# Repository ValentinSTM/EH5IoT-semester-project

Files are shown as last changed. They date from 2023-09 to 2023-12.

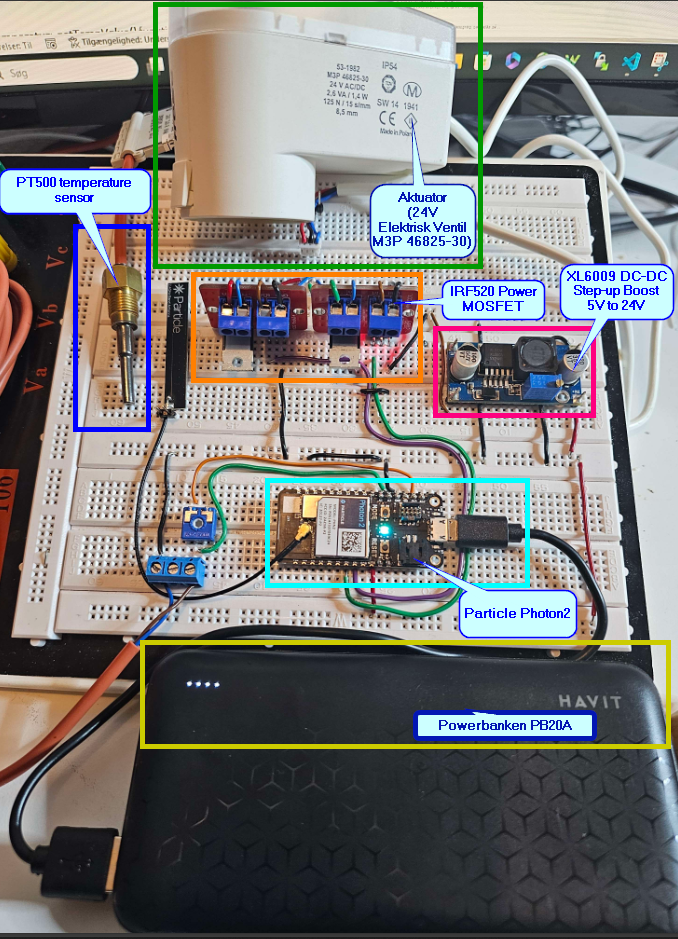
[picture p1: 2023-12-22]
Docs_Tests/Realisering-.png

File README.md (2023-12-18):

# EH5IoT-semester-project
The IoT semester project - Return Temperature Regulation for Fjernvarme
## Table of Contents
- [General Info](#general-info)
- [Technologies](#technologies)
- [Requirements](#requirements)
  - [Functional Requirements](#functional-requirements)
  - [Non-functional Requirements](#non-functional-requirements)

## General Info
This project focuses on optimizing the return temperature in Heating System District ( Fjernvarme ) to enhance energy efficiency and promote environmental sustainability. In collaboration with Kredsløb A/S, we strive to maintain return temperatures below 30°C, which qualifies for a bonus.

"Få styr på din fjernvarme og spar penge på din varme

Vidste du, at du kan spare penge på din varmeregning og samtidig bidrage til mere klimavenlig fjernvarme? Hemmeligheden ligger i det, der hedder returtemperatur og god udnyttelse af energien.
Det er temperaturen på det fjernvarmevand, der bliver sendt retur fra dit hjem til varmeværket.
Og er returtemperatur fra din bolig under 30°C, får du en bonus." (www.kredslob.dk)

### About Fjernvarme
Fjernvarme is a district heating system that supplies heat to multiple households from a centralized source. The return temperature refers to the temperature of the water sent back from homes to the heating plant.

### Project Implementation
This system was implemented using one Particle Photon2 board, leveraging IoT technology to gather data from weather forecasts webhook and changing temperature setpoint after those data as seen in the tabel. 
Logic for temperature setpoint is dynamic depending on the outside temperature.

| Temperature Condition | Set Point  |
|---|---|
| Extreme low temperature (< -3°C) | 40°C |
| Low temperature (-2°C to 2°C) | 35°C |
| Normal temperature (> 3°C) | 30°C |

The system will collect data from a temperature sensor RTD PT500 Kamstrup mounted on return pipe .
Data collected from the temperature sensor will by used in an PID controller (Proportional, Integral, Derivative ) able to control the dynamic system, by giving som resultat a parameter to adjust the position of an electro valve. 
- P = Proportional - Kp = Proportional constant (adjust current error)
- I = Integral - Ki = Integral constant ( adjust past error)
- D = Derivative - Kd = Derivative constant (adjust future error)

## Technologies
The following technologies are used in this project:
- Particle Photon2 for data acquisition and actuator control
- Temperature Sensor: PT500 Kamstrup
- Actuator: 24V Electric Valve M3P 46825-30
- IoT: Webhooks for weather forecast data

## Requirements
### Functional Requirements
The device must meet the following functional requirements:
- Establish an internet connection via Wi-Fi
- Read data from the connected PT500 temperature sensor
- Control the electric valve actuator
- Utilize data from a web service, such as weather forecast data to help in controlling the system.

### Non-functional Requirements

- Create a public GitHub account and upload relevant project files.
- Upload hardware documentation, schematics, datasheets, and optional PCB layouts in PDF format.
- Upload software files in raw source code format, such as .C, .CPP, .h, .py, etc.

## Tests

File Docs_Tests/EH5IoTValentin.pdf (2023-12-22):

# Valentin-Stefan Tudora-Mayer Studienummer: 202104813

# EH5 IoT projekt

# Optimering af returtemperatur i fjernvarmesystemer ved brug af IoT-teknologi

### S i d e 1 | 24

Dato: 21. december 2023

Kursus: EH5IoT
Navn / Studienummer:
Valentin-Stefan Tudora-Mayer / 202104813

## Indhold

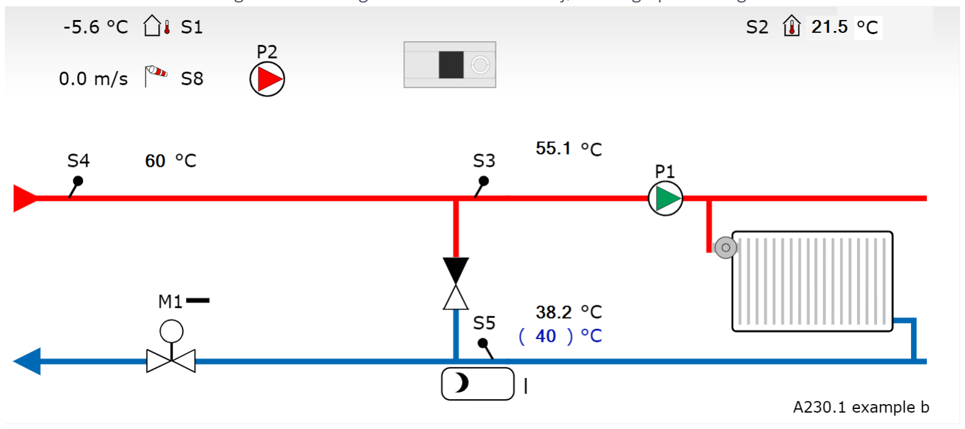
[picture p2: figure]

### S i d e 2 | 24

## Introduktion

Dette projekt, EH5IoT-semesterprojektet, koncentrerer sig om optimering af returtemperaturen i fjernvarmesystemer for at øge energieffektiviteten og fremme bæredygtighed. Samarbejdet med Kredsløb A/S understreger vores mål om at opretholde returtemperaturer under 30°C, hvilket kvalificerer til en økonomisk bonus. Vores initiativ adresserer det voksende behov for klimavenlige løsninger i fjernvarmesektoren, et kritisk element i overgangen til mere bæredygtige energisystemer.

Målet med EH5IoT-semesterprojektet er at anvende Internet of Things (IoT)-teknologi for at præcist regulere og optimere returtemperaturen i fjernvarmesystemer. Ved at integrere avanceret sensorik og intelligent styring, sigter vi mod at forbedre systemets samlede energieffektivitet, reducere driftsomkostninger for slutbrugere og bidrage til et mere miljømæssigt ansvarligt fjernvarmesystem.

Løsningen involverer implementering af et IoT-baseret system, der bruger Particle Photon2-board til at indsamle data og styre en aktuator. Systemet vil anvende data fra vejrprognoser til dynamisk at justere setpunkterne for returtemperaturen, baseret på udendørs temperaturforhold. Ved hjælp af en RTD PT500 Kamstrup-temperatursensor monteret på returrøret, vil systemet indsamle nøjagtige data, der bruges af en PID-controller (Proportional, Integral, Derivative) til at styre en elektrisk ventil effektivt. Denne innovative tilgang tillader præcis kontrol og tilpasning af systemet i realtid, hvilket øger effektiviteten og understøtter en mere bæredygtig energianvendelse.

## Projektbeskrivelse

Fjernvarme er et centraliseret varmesystem, der leverer varme til flere husstande. I dette system er returtemperaturen
- temperaturen på vandet, der sendes tilbage fra boligerne til varmeværket - afgørende for systemets effektivitet. En lavere returtemperatur betyder, at mere varme er blevet udnyttet i boligerne, hvilket fører til en højere effektivitet og lavere energiforbrug.

I dette projekt, i samarbejde med Kredsløb A/S, er der et specifikt fokus på at opretholde returtemperaturen på 30°C, mens indgangstemperaturen, der garanteres af Kredsløb A/S, er på 60°C (Figur 1). Dette temperaturinterval er afgørende for at sikre maksimal udnyttelse af den leverede varmeenergi. For eksempel, en reduktion i returtemperaturen fra 35°C til 30°C, mens indgangstemperaturen forbliver på 60°C, betyder en forbedring i energieffektiviteten.

Optimeringen af returtemperaturen er derfor afgørende for at forbedre fjernvarmesystemets overordnede energieffektivitet og for at reducere de miljømæssige påvirkninger.

Figur 1 [1]Fjernvarme flowdiagram (Kilder - Kredsløb A/S - ECL portal)

### S i d e 3 | 24

### Beskrivelse af systemets hovedkomponenter

Systemet blev udviklet til dette formål og omfatter flere nøglekomponenter:

1. Particle Photon2: Dette er en mikrocontroller, der fungerer som kernen i IoT-løsningen. Den indsamler data fra forskellige sensorer og styrer aktuatorer baseret på foruddefinerede logikker og eksterne datainput. En afgørende funktion ved Particle Photon2 er dens evne til at forbinde til internettet, hvilket muliggør fjernovervågning og -styring af systemet. Takket være Particles integrerede cloud-tjenester, kan systemet nemt tilgå og anvende data fra eksterne kilder, såsom vejrprognoser, hvilket spiller en nøglerolle i projektet. Denne forbindelse til internettet udvider systemets funktionalitet betydeligt og tillader en mere fleksibel og effektiv styring af fjernvarmesystemet.
2. Temperatursensor PT500 Kamstrup: Denne sensor er monteret på returrøret og måler returtemperaturen med præcision. Disse data er afgørende for at regulere og vedligeholde den optimale returtemperatur.
3. Aktuator (24V Elektrisk Ventil M3P 46825-30): Denne bruges til at justere vandstrømmen og dermed returtemperaturen baseret på data og kommandoer fra Particle Photon2 og PID-controlleren.

Logikken implementeret for temperaturregulering.
Systemet anvender en dynamisk logik til temperaturregulering, som er afhængig af eksterne temperaturforhold. En PID-controller (Proportional, Integral, Derivative) anvendes, som justerer ventilens position for at opnå den ønskede returtemperatur. Controlleren modtager input fra temperatursensoren og justerer aktivt ventilen baseret på tre parametre:
- Proportional (P): Justerer den aktuelle fejl.
- Integral (I): Akkumulerer tidligere fejl for at forbedre stabilitet over tid.
- Derivative (D): Forudsiger fremtidige fejl og reagerer på ændringer.

Ved at integrere realtidsdata fra sensorer og vejrprognoser, kan systemet proaktivt justere set punkterne for returtemperaturen, hvilket sikrer maksimal effektivitet under alle driftsforhold.

## Kravs analyse

Krav
ID | Kategori | Beskrivelse

Godkendt/Ikke
godkendt | Kommentarer
F.1 | Funktionelt

Enheden skal forbinde til internettet via
WiFi. | Godkendt

AU's "AU Gadget netværk" er testet og fungerer.

F.2 Funktionelt

Enheden skal aflæse data fra PT500-
sensoren, som måler temperatur og
implementerer datatfiltrering. | Godkendt

PT500 sensoren er
implementeret og funktionalitet bekræftet via tests.

F.3 Funktionelt

Enheden skal kunne styre en aktuator,
som er reguleret af en PID-controller. Godkendt

PID-reguleringen er
implementeret og justeret
baseret på tests.

### S i d e 4 | 24

Krav
ID | Kategori | Beskrivelse

Godkendt/Ikke
godkendt | Kommentarer
F.4 | Funktionelt

Enheden skal integrere og anvende data
fra eksterne webtjenester til at forbedre
dens funktionalitet. | Godkendt

Integration af webhooks og API'er for vejrdata er testet og implementeret.

F.5 Funktionelt

Data skal sendes til clouden i en log med
defineret interval og størrelse for at
monitorere systemets ydeevne. | Godkendt

Data logning og transmission er implementeret og fungerer som forventet.

F.6 Funktionelt

Aktuatoren skal kunne modtage strøm
fra en batterikilde ved hjælp af en DC-DC
boost step-up konverter. | Godkendt

Implementeringen og tests af DC-DC konverteren har bekræftet korrekt funktion.

IF.1

Ikke-funktionelt

Offentlig GitHub-repository med alle
relevante filer. | Godkendt

Repository er aktivt og offentligt tilgængeligt.

IF.2

Ikke-funktionelt

Hardware dokumentation inklusiv
skematikker og datablade skal uploades i
PDF-format. | Godkendt

Komplet dokumentation er
tilgængelig og godkendt.

IF.3

Ikke-funktionelt

Software kildekoden skal uploades i rå
format. | Godkendt

Kildekoden er tilgængelig i repository og er blevet
gennemgået.

T.1 Teknisk

Den indlejrede platform skal være en
Particle-enhed med WiFi-forbindelse. | Godkendt | Particle-enhed valgt og testet.
T.2 | Teknisk

Platformen skal have digitale/analoge
I/O'er for sensor- og
aktuatorforbindelser. | Godkendt

I/O-specifikationer er opfyldt og fungerer som forventet.

T.3 Teknisk

Systemet skal kunne drives af batteri, ud
over USB 5V strømforsyning. | Godkendt

Batteridrift er testet og klar til yderligere overvågning for at optimere levetiden.

T.4 Teknisk

Batteriets levetid og systemets samlede energiforbrug skal evalueres for at
estimere driftstiden ved fuld
batteriopladning. | Godkendt

Yderligere langvarige tests og overvågning nødvendige for at fastlægge nøjagtig batterilevetid.

Bemærk, at selvom alle kravene er markeret som "Godkendt", indikerer kommentaren for T.4, at der stadig er behov for yderligere langvarige tests og overvågning for præcist at bestemme batteriets levetid, især fordi aktuatoren har et højere strømforbrug under drift, hvilket er kritisk for den overordnede energieffektivitet og anvendelighed af systemet i områder uden elektrisk strømforsyning.

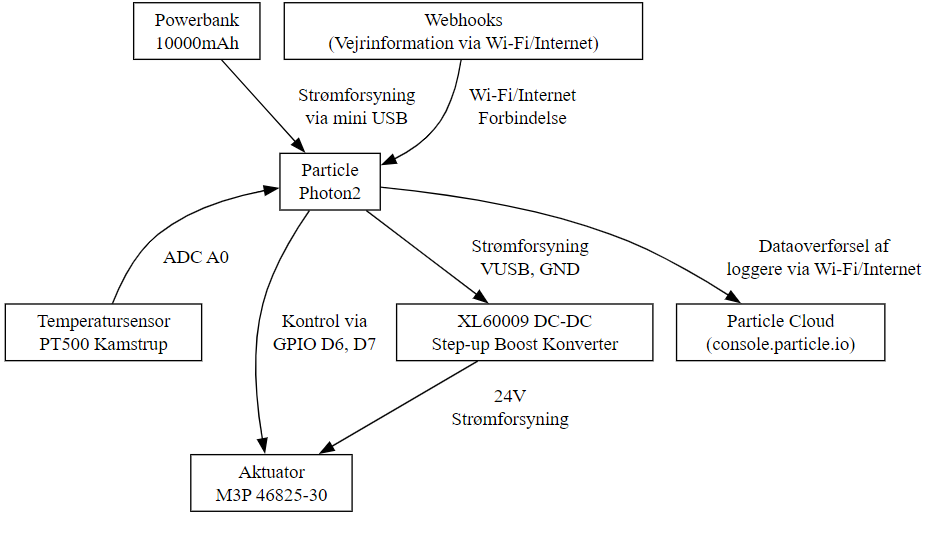
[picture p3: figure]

### S i d e 5 | 24

## Systemdesign

Systemets diagram.

Figur 2 System Block Diagram

## Hardware

- Particle Photon2 (Figur 3 og Figur 4 [2]) er en avanceret mikrocontroller modul designet til Internet of Things (IoT) applikationer som tilbyder :
- MCU & Processor: Realtek RTL8721DM, ARM Cortex M33, 200 MHz.
- Hukommelse: 2 MB Flash, 3 MB RAM.
- Wi-Fi: Dual-band 2.4 GHz & 5 GHz, BLE 5 support.
- Antenne: Integreret PCB, U.FL for ekstern antenne.
- I/O Porte: 6x ADC, 3x UART, 2x SPI, I2C-kommunikation.
- Strømstyring: Understøtter LiPo-batteri, USB-strøm.
- Lavenergimodes: Effektive sleep modes for strømbesparelse.
- Firmware: Over-the-air opdateringer, Device OS 5.0.0+.

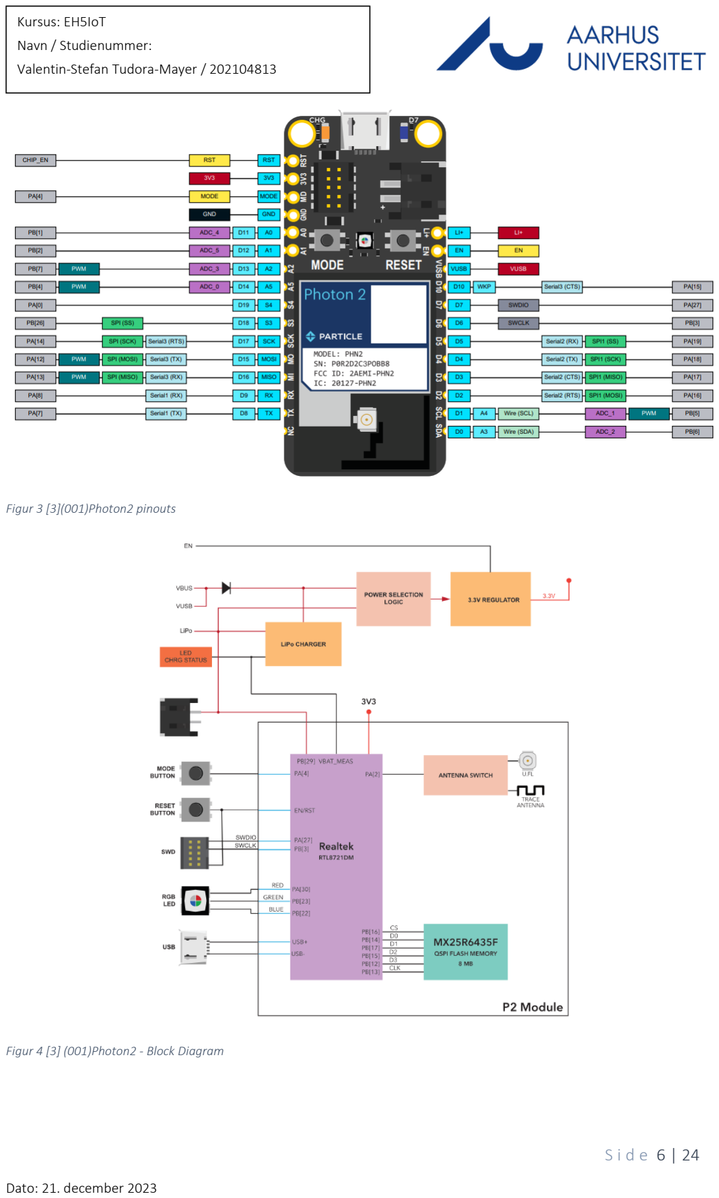
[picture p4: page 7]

### S i d e 6 | 24

Figur 3 [3](001)Photon2 pinouts

Figur 4 [3] (001)Photon2 - Block Diagram

### S i d e 7 | 24

- PT500 er en 2-leder resistiv temperaturføler(Figur 6), anvendt til nøjagtig måling af temperaturen i fjernvarmesystemer. PT500 temperaturføleren, ofte anvendt i varme- og kølesystemer, bruger tyndfilmsmodstande monteret på et trykt kredsløbskort (PCB). Tyndfilmsmodstande er valgt for deres omkostningseffektivitet, kompakthed og hurtige respons på temperaturændringer. Denne konstruktion tillader massekproduktion og reducerer omkostninger. Med loddeøer på PCB, er det let at forbinde to ledninger til en 2-leder temperaturføler, hvilket optimerer fremstillingsprocessen. PT500 sensoren kan typisk bruges op til 150 °C, hvilket er tilstrækkeligt for de fleste installationer.
Sensoren har følgende karakteristika:
- Modstandsændring: Sensoren benytter platin med en temperaturkoefficient på 0,00385 ohm/ohm/°C, hvilket sikrer en præcis og næsten lineær respons til temperaturændringer.
- Tabelbaseret beregning: Til konvertering af modstandsværdier til temperaturer anvendes en standardtabel, som er integreret i systemets software. Dette sikrer en høj grad af nøjagtighed i temperaturbestemmelsen.
- 2-leder konfiguration: Selvom PT500 også er tilgængelig i 4-leder konfigurationer for endnu større nøjagtighed, anvendes en 2-leder konfiguration i dette projekt

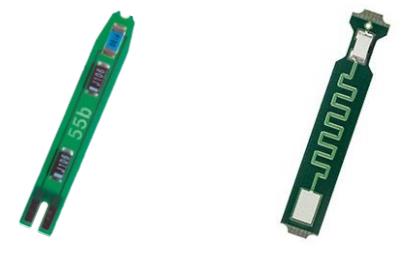
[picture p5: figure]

Figur 5 [3](002)Tyndfilmsmodstande, som er monteret på et PCB (printed circuit board)

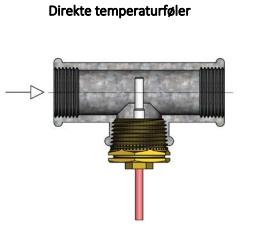
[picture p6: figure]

Figur 6 [3](002)Illustration af en direkte temperaturføler

### S i d e 8 | 24

- M3P 46825-30 aktuatoren (Figur 7)er en motoriseret aktuator til regulering af flow i varme- og kølesystemer. Tekniske specifikationer inkluderer:
- Kontroltype: 3-punkts kontrol uden feedback.
- Driftsspænding: 24 V AC, -10 % ... +20 %, 50-60 Hz 24 V DC, -20 % ... +20 %
- Driftseffekt: 0,2 W...1,4 W (DC), 0,56 VA...2,6 VA (AC)
- Strømforbrug (M3P): < 110 mA
- Indstillingsvej: 8,5 mm
- Indstillingskraft: 100/125/150/200 N -20 % ... +40 %
- Indstillingstid: 15s, 30s s/mm
- Omgivelsestemperatur: 0 °C ... +50 °C
- Beskyttelsesklasse: IP 54 i henhold til EN 60529.
- Kontrolsignal: 3-punkts signal.
- Denne aktuator er central i projektet for at præcist justere ventilpositionen, hvilket direkte påvirker returtemperaturen i opvarmningssystemet, og bidrager til at forbedre systemets energieffektivitet.

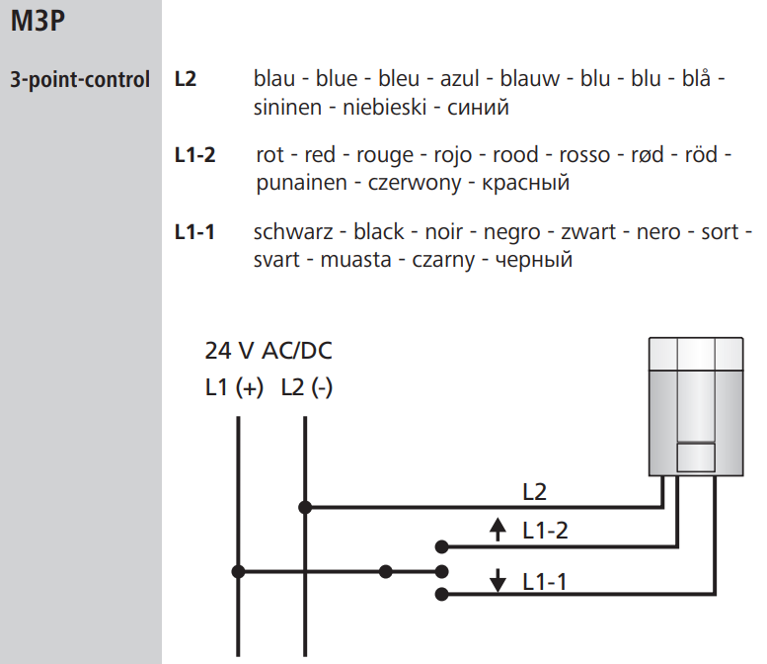
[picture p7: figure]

Figur 7 [3](003) Elektrisk diagram

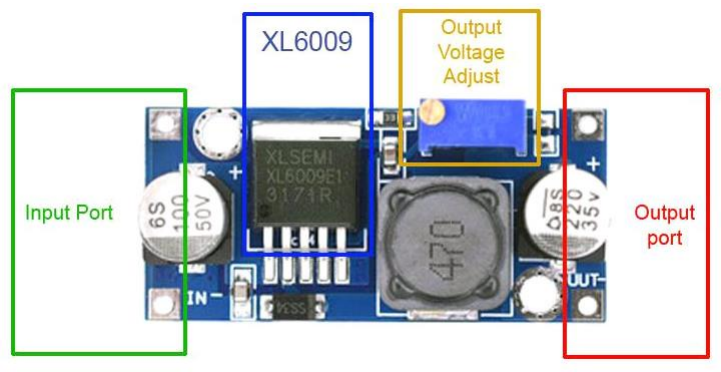
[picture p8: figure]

### S i d e 9 | 24

- Powerbanken PB20A (Figur 8), anvendt i projektet, til at forsyne med strøm , har følgende nøgleegenskaber:
- Kapacitet: 10.000 mAh, 3,7 V, 37 Wh, hvilket sikrer tilstrækkelig strøm til langvarig brug af systemet.
- Indgang og Udgang: Udstyret med USB-C-indgang (5 V/2 A) og USB-A-udgang (5 V/2 A), der tilbyder alsidige opladningsmuligheder og høj kompatibilitet med forskellige enheder.
- Sikkerhedsfunktioner: Inkluderer overladningsbeskyttelse og automatisk slukning efter fuld opladning, hvilket sikrer både powerbankens og tilkoblede enheders sikkerhed.

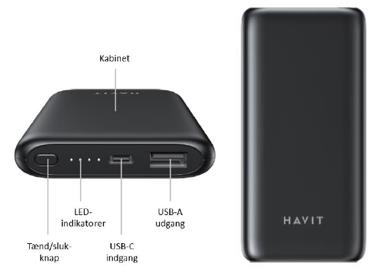
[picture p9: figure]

Figur 8 [3](004) Powerbank

- XL6009 DC-DC (Figur 9): Specifikationer og egenskaber for strømmodul til at levere strøm til en 24V aktuator:
- Indgangsspænding: 3 - 32V.
- Udgangsspænding: Justerbar fra 5 - 35V.
- Udgangsstrøm: Maksimal udgangsstrøm 4A. Bemærk: Jo højere spændingen er, desto større bliver belastningsstrømmen.
- Effektivitet: Op til <94% effektivitet.
- Belastningsregulering: 0,5%.
- Spændingsregulering: 0,5%.
- Justerbar potentiometer: Ombord for justering af udgangsspændingen.

Figur 9 [3] (005) XL6009 DC-DC Convertor module

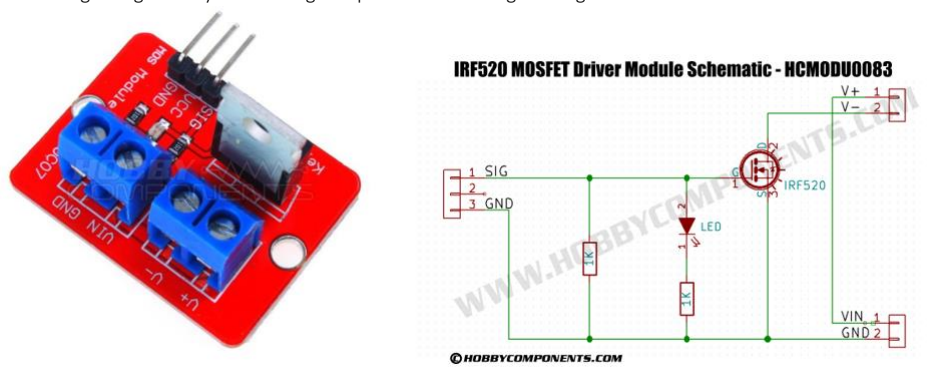
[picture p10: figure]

### S i d e 10 | 24

- IRF520 (Figur 10) Power MOSFET N-Channel modulen benytter en IRF520 Power MOSFET for at styre og regulere PWM-signaler til belastninger som DC-motorer og magnetventiler.
- Modulen kan håndtere en udgangsspænding på 0-24V og en udgangsstrøm på op til 9,5A. For strømme over 1A kræves en ekstra køleplade. Den understøtter gate-spændingssignaler på både 3,3V og 5V og er forsynet med digitale porte til niveau-signalering.

Figur 10 [4](006) IRF520 Modulen og Skematik

Grænseflade og kommunikation mellem komponenter.

## Implementering

Udviklingsprocessen for hardware og software.
Implementeringsfasen i EH5IoT-projektet omhandler integration og konfiguration af hardware og softwarekomponenter for at skabe et fungerende IoT-system som skal afleveres en retur temperatur som er indstillet på setpoint.

Det inkluderer etablering af forbindelser mellem komponenter som Particle Photon2, PT500 temperatursensoren, M3P 46825-30 aktuatoren, powerbanken , XL6009 DC-DC konverteren og IRF520 Power MOSFET. Under denne fase er der lagt vægt på at sikre korrekt energioverførsel, dataindsamling og -behandling samt effektiv kommunikation mellem systemets dele. Desuden er der udviklet software til at styre og regulere systemet baseret på realtidsdata og prædefinerede algoritmer.

Prototypen til projektet blev udviklet på et eksperimentbræt (breadboard), hvor en PCB ikke var nødvendig. Systemets strømforsyning kommer fra en powerbank, der leverer 5V via USB til Particle Photon2-platformen. Fra Particle Photon2's Vusb-pin leveres strøm til XL6009 DC-DC-modulet, som konverterer spændingen op til de nødvendige 24V for aktuatoren M3P 46825-30. Alternativt kunne en SAFT longlife-batteri bruges, der ofte anvendes i fjernvarmeapplikationer og industrielle miljøer.

Aktuatoren styres digitalt fra Photon2's pins D6 og D7, via to IRF520 Power MOSFET-moduler, som understøtter gate-spændingssignaler på 3,3V og 5V og kan håndtere en udgangsspænding på 0-24V og en udgangsstrøm på op til 9,5A. Temperaturen setpoint styres dynamisk baseret på vejrprognoser hentet via en webhook, med sætpunkter på 30, 35 eller 40 °C.

Temperature Condition | Set Point
Extreme low temperature (< -3°C) | 40°C
Low temperature (-2°C to 2°C) | 35°C
Normal temperature (> 3°C) | 30°C
Tabel 1 Setpoint temperature

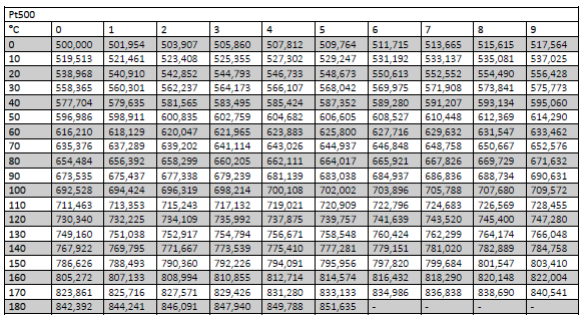
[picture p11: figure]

### S i d e 11 | 24

Returtemperaturen registreres ved hjælp af en PT500 temperatursensor, som er tilsluttet mellem A0-pinden på en Photon2, GND, og en 1k Ohm variabel modstand. Dette setup gør det muligt at beregne resistansen af PT500-sensoren. PID-regulatoren tilpasser herefter aktuatoren bevægelserne for at holde den ønskede temperatur, baseret på feedback fra PT500-sensoren. Værdien af Pt500 beregnes ved brug af en tabel (Tabel 2) over resistansværdier, som svarer til forskellige temperaturer, leveret af sensorens producent, Kamstrup A/S.

Tabel 2 [3] - Pt500, IEC 751 Amendment 2-1995-07

Hardware

Figur 11 Implementering skematik


### S i d e 12 | 24

Software

Softwarekomponenterne i projektet arbejder sammen for at regulere og overvåge fjernvarmesystemets returtemperatur. Kernen i softwarelogikken er en PID-controller, som dynamisk justerer en aktuators position baseret på feedback fra en PT500 temperatursensor. Temperaturen læses og jævnes ud gennem en glidende gennemsnitsfunktion for at sikre stabil drift.

Vigtige funktioner i softwaren omfatter indsamling af temperaturdata, kommunikation med vejrprognoser og systemets interaktion med Particle Cloud for at logge og overvåge ydeevnen. PID-controllerens konstanter (Kp, Ki, Kd) er defineret for at balancere systemets respons mellem nuværende, akkumuleret og forventet temperaturafvigelse. Systemet håndterer også intervalbaserede opgaver som indsamling og offentliggørelse af data samt opdatering af setpoint temperature baseret på vejrforudsigelser som er beskrevet i Tabel 1.

Hele implementeringen er trådbaseret for at sikre kontinuerlig og uafhængig håndtering af de forskellige systemopgaver. Koden er skrevet i C++ og gør brug af Particle's udviklingsmiljø og biblioteker. For detaljeret gennemgang og yderligere teknisk indsigt, kan koden tilgås på GitHub [5].

Figur 12Forsimplet Software Diagram

### S i d e 13 | 24

### Setup function

På diagrammet kan man se opsætningsproceduren, som skal køres før man går ind i hovedløkken. Vi initialiserer seriel kommunikation til brug for logning. Logning er blevet brugt omfattende gennem udviklingsprocessen til fejlfinding. Particle understøtter flere logniveauer, og programmet er i øjeblikket indstillet til at logge alle INFO beskeder. Dernæst initialiseres GPIO'erne for både temperatursensoren (som analog indgang) og aktuatoren (som digital udgang). Vi abonnerer på vejr-begivenheden, og navnet på begivenheden vil senere blive brugt af Particle Cloud til at sende data tilbage. Her specificerer vi også callback-funktionen til at fortolke de modtagne data. Aktuatoren kalibreres derefter, dette er for at sikre, at vi starter programmet fra en kendt position af aktuatoren. Aktuatoren vil bevæge sig helt op (100% åben) og lukke ned til frostbeskyttelsespositionen (5%). Denne proces er tidskrævende, kan tage op til 4 minutter. Af denne grund tilføjede jeg et debug-flag for at deaktivere kalibrering under udviklingen. Til sidst starter vi valveControlThread, så den vil være klar til at bruge outputtet fra PID-controlleren. PID-controlleren initialiseres også her: outputområdet (0-100), det indledende setpunkt (30) og funktionsmåden (Automatisk).


Figur 13 Setup Flow Chart

### S i d e 14 | 24

### Main loop (main thread)

Funktionaliteten af hovedtråden er ret simpel, da den kun læser temperatursensoren og giver dette som input til PID-controlleren. Vi gemmer resultatet af PID-controllerens beregning i en global variabel, som skal bruges i den anden tråd. Af denne grund er vi nødt til at bruge en mutex og låse den, før vi manipulerer med variablen. Resten af funktionaliteten i hovedløkken består af logning af data, at sende disse data til skyen, at anmode om vejrudsigt og bruge udsigten til at konfigurere setpunktet. Alt dette sker ved foruddefinerede tidsintervaller, som ses i følgende tabel. Til sidst har vi en forsinkelsesfunktion på 1 sekund.

Aktion | Tids interval
Saml log data | 1 time
Publish log data | 3 timer
Request vejrudsigt | 3 timer
Beregn og update setpoint til PID | Dataen skal være nyere end 3 timer


Figur 14 Main Loop Flow Chart

### S i d e 15 | 24

### Aktuator kontrol thread

Den anden tråd i applikationen håndterer styringen af aktuatoren. Aktuatornes nuværende position er gemt i en variabel. Vi læser den globale variabel for den nye position beregnet af PID-controlleren. Og vi beregner forskellen mellem de to for at finde ud af, hvilken retning aktuatoren skal bevæge sig. Baseret på dette vil vi enten åbne eller lukke aktuatoren ved hjælp af de to digitale GPIO'er. Problemet er dog, at denne proces er ret langsom. Dette var en af de væsentligste grunde til at flytte aktuatorfunktionaliteten til en separat tråd – for at undgå at have en stor mængde forsinkelser i hovedtråden. Hvis PID-controlleren siger, at aktuatoren ikke behøver at bevæge sig, vil tråden sove i et sekund.


Figur 15Valve_control_thread_flow_chart


### S i d e 16 | 24

### Weather forecast functionality

Kommunikationen med openweathermap API foretages af Particle Cloud, ved hjælp af deres Integrations-funktionalitet. Vi har brug for timebaserede data, så dette skulle specificeres i forespørgslen til openweathermap. Dette kan gøres i konfigurationen af Integrationen, hvor du også skal specificere placeringen, måleenhederne og API-nøglen.

En meget fin funktion ved Particle Integration er, at den kan filtrere dataene for os. Ved det første forsøg på at håndtere data direkte fra openweathermap indse jeg, at jeg ikke kunne håndtere mængden af data, der blev sendt (48 datasæt for de følgende 48 timer). Følgende "Response Template" bruges til kun at filtrere de data, vi er interesserede i (de næste 3 timer).

Når jeg modtager dataene på Particle Photon, har jeg brugt en funktion genereret på https://docs.particle.io/integrations/webhook-demo/ til at dekode JSON-objekterne.


### S i d e 17 | 24

Figur 16 Realisering af IoT prototype på breadboard

### S i d e 18 | 24

## Test og Verifikation


Figur 17Test calibration - valve change direction


Figur 18 Test calibration finish antifreeze position

Figur 19 Test calibration forecast Particle


### S i d e 19 | 24

Figur 20 Test calibration forecast Cloud

Figur 21Test individual data log save

Figur 22 Test data log Particle

### S i d e 20 | 24


Figur 23 Test data log Cloud


### S i d e 21 | 24

Figur 24 Test temperature increase

Figur 25 Test temperature decrease


### S i d e 22 | 24

Figur 26 Test change setpoint based on weather forecast

## Projekt konklusion

### 1. Projektets Resultater

- EH5IoT-projektet har opnået sit hovedmål om at optimere returtemperaturen i fjernvarmesystemer ved brug af IoT-teknologi.
- Integrationen af Particle Photon2, Kamstrup PT500 temperatursensoren og effektiv PID-logik har muliggjort præcis regulering af returtemperaturen til under 30°C.
- Anvendelsen af vejrprognosedata har forbedret temperaturreguleringen og bidraget til øget energieffektivitet og reducerede omkostninger.

### 2. Impact på Effektiviteten af Fjernvarmesystemet

- Systemet har forbedret energieffektiviteten signifikant ved at vedligeholde en lav returtemperatur, hvilket resulterer i en mere effektiv brug af termisk energi.
- En nedgang i energiforbruget og en reduktion af miljøpåvirkningen har understøttet bæredygtighedsindsatser og reduceret kulstofudledningen.

### 3. Udfordringer og Lærte Lektioner

- En væsentlig udfordring var at sikre effektiv og stabil kommunikation mellem systemkomponenterne, hvilket nødvendiggjorde finjustering af software og hardware.
- Grundig testning og tilpasningsevne har været afgørende i implementeringen af IoT-løsninger, idet projektet præsenterede kontinuerlige nye udfordringer og læringsmuligheder.

### 4. Forslag til Forbedringer og Fremtidige Udvidelser

- Vi vil fremover udforske mulighederne for at opdele applikationen i tråde for at forbedre respons og effektivitet, samt konvertering af eksisterende kode til C++ klasser for bedre struktur og vedligeholdelse.
- Energiopsparingsfunktioner og forbedret batteristatusindikation, som FuelGauge FuelGauge, vil blive integreret for at forlænge systemets levetid og pålidelighed.
- Implementering af en antifryse-funktion vil yde beskyttelse ved lave batteriniveauer, aktiveret kun når vejrudsigten viser negative temperaturer.
- Vi planlægger at anvende timer interrupts til forsinkede begivenheder, hvilket potentielt kan forbedre energisparetiltag.

### S i d e 23 | 24

- Yderligere vil vi beslutte præcist, hvilke data vi vil logge, herunder ventiltemperatur, nuværende udetemperatur, og ventilbevægelser, samt formatet og perioden for afsendelse til skyen for optimal overvågning og vedligeholdelse.
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

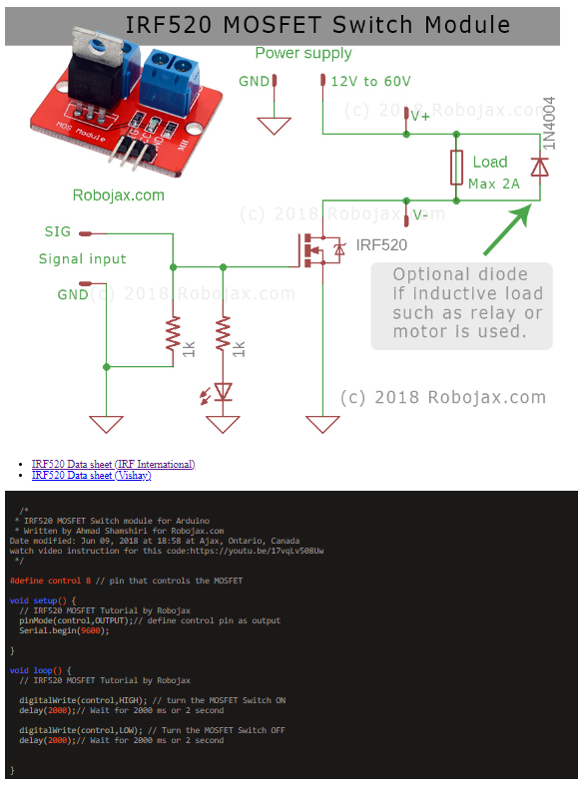
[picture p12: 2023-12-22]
Docs_Tests/Docs/006_ IRF520 MOSFET .png

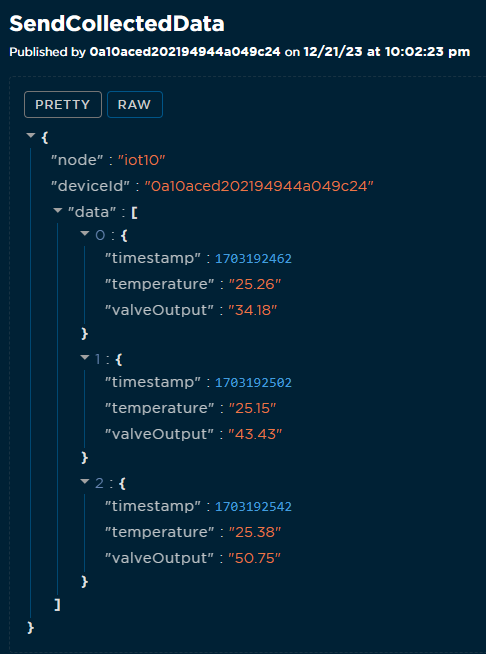
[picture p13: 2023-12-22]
Docs_Tests/test_data_log_cloud.png

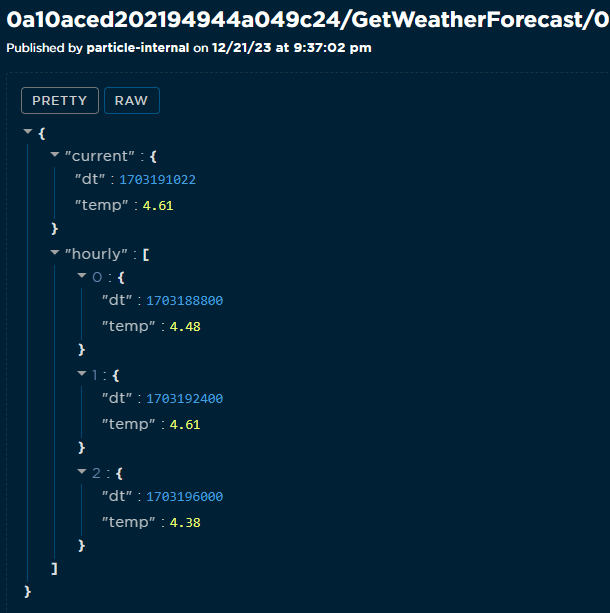
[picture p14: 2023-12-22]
Docs_Tests/test_calibration_forecast_cloud.png

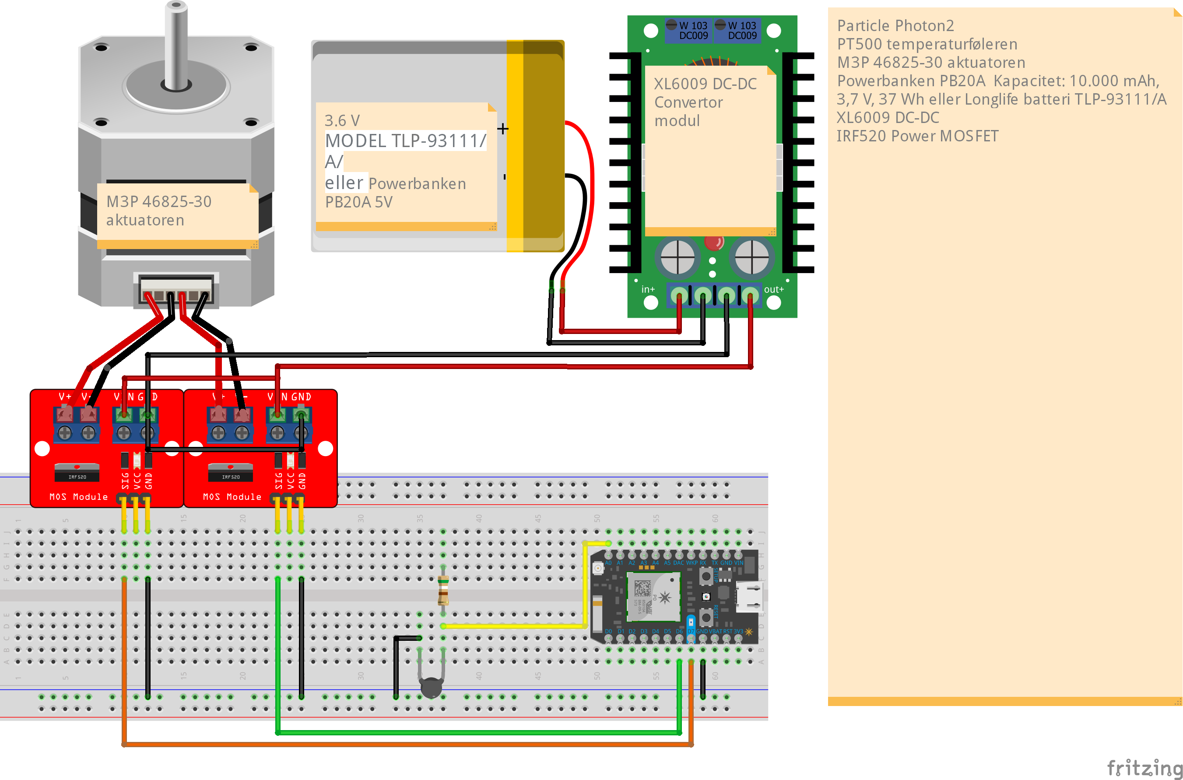
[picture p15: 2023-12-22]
Docs_Tests/IoTSkematik2_bb.png

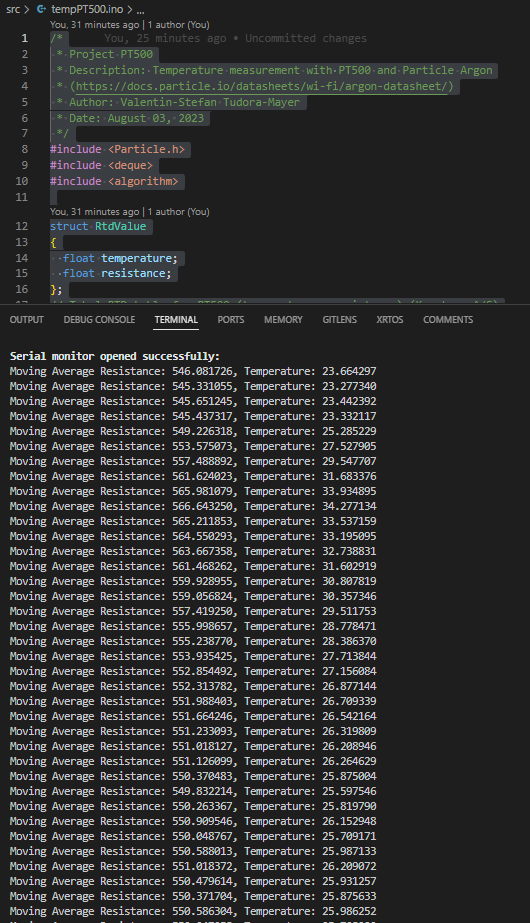
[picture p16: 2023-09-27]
Docs_Tests/PT500.png

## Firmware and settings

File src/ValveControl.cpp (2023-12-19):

// ValveControl.cpp

#include "ValveControl.h"
#include "application.h" // Include Particle specific functions
#include "Common.h"

const int PIN_VALVE_OPEN = D6;  // Valve opening pin
const int PIN_VALVE_CLOSE = D7; // Valve closing pin

const unsigned long totalValveOpenTime = 8.5 * 15 * 1000;   // Total time required for full opening (8.5 mm * 15 seconds/mm)
const unsigned long stepValveTime = 8.5 * 15 * 1000 * 0.01; // We define a step of 1% of the total time required for full opening (1% of 8.5 mm * 15 seconds/mm)
unsigned int currentStep = 0;                               // Current step in the valve control algorithm, from 0 to 100

// Valve control pin initialization function
void setupValveControl()
{
    pinMode(PIN_VALVE_OPEN, OUTPUT);  // Set the opening valve pin as output
    pinMode(PIN_VALVE_CLOSE, OUTPUT); // Set the closing valve pin as output
}

// Valve opening function
void openValve()
{
    digitalWrite(PIN_VALVE_OPEN, HIGH); // Open the valve
    digitalWrite(PIN_VALVE_CLOSE, LOW); // Stop the valve
    Log.info("Opening valve...");       // Print to the serial monitor
}

// Valve closing function
void closeValve()
{
    digitalWrite(PIN_VALVE_CLOSE, HIGH); // Close the valve
    digitalWrite(PIN_VALVE_OPEN, LOW);   // Stop the valve
    Log.info("Closing valve...");        // Print to the serial monitor
}

// Valve stop function
void stopValve()
{
    digitalWrite(PIN_VALVE_OPEN, LOW);  // Stop the valve
    digitalWrite(PIN_VALVE_CLOSE, LOW); // Stop the valve
    Log.info("Stop valve...");          // Print to the serial monitor
}

void valveControlThread(void)
{
    while (true)
    {
        os_mutex_lock(valveMutex);
        double localValveOutput = valveOutput;
        os_mutex_unlock(valveMutex);
        controlValve((unsigned int)localValveOutput);
    }
}

void controlValve(unsigned int steps)
{
    int noOfSteps = steps - currentStep;
    Log.info("Step difference to move valve: %d", noOfSteps);

    if (noOfSteps > 0)
    {
        openValve();
        waitForSteps(noOfSteps);
        stopValve();
    }
    else if (noOfSteps < 0)
    {
        closeValve();
        waitForSteps(noOfSteps);
        stopValve();
    }
    else
    {
        delay(1000); // keep the tread alive with normal delay funtion, we don't really care about drift
    }
}

void waitForSteps(int steps)
{
    unsigned int stepsToMove = abs(steps);

    while (stepsToMove--)
    {
        delay(stepValveTime);

        if (steps > 0)
        {
            currentStep++;
        }
        else
        {
            currentStep--;
        }

        Log.info("Current step: %d", currentStep);
    }
}

// Valve calibration function
void calibrateValveOnStartup()
{
    if (enableCalibration)
    {
        controlValve(VALVE_MAX_SETTING); // Open the valve to maximum

        controlValve(VALVE_ANTIFREEZE_SETTING); // Close the valve down to antifreeze point
    }
}

// Valve control anti freeze function ensuring that the valve is open at least 5%
void ensureAntiFreeze()
{
    controlValve(VALVE_ANTIFREEZE_SETTING);
}

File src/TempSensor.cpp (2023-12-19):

// TempSensor.cpp
#include "TempSensor.h"
#include "RTDTable.h" // Include the RTD Table module header file
#include <algorithm>  // Add this to include the standard algorithms library

std::deque<float> temperatureSamples; // Queue of temperature samples for moving average calculation

void setupTempSensor()
{
    pinMode(ANALOG_PIN, INPUT); // Set an analog pin (A0) as an input pin for the ADC (Analog to Digital Converter) to read the sensor data from the PT500 RTD sensor (resistance)
}

int readTempSensor()
{
    return analogRead(ANALOG_PIN); // Read the analog value from the sensor
}

float calculateResistance(int adcValue) // Function to convert the analog value to resistance
{
    float voltage = (adcValue / ADC_MAX_VALUE) * REFERENCE_VOLTAGE; // Calculate the voltage from the ADC value
    return SERIES_RESISTOR / ((REFERENCE_VOLTAGE / voltage) - 1.0); // Calculate the resistance from the voltage
}

float getTempValue()
{
    int sumOfSamples = 0;
    int noOfSamples = 10;

    // Read the temperature from the PT500 sensor, and make an average of 10 samples to get a stable reading
    for (int i = 0; i < noOfSamples; i++)
    {
        sumOfSamples += readTempSensor();
        delay(10);
    }

    int averageAdcValue = (int)(sumOfSamples / noOfSamples);
    float resistance = calculateResistance(averageAdcValue);
    float temperature = interpolateTemperature(resistance);

    // Moving average for spikes over longer time periods
    float averaged_temperature = calculateMovingAverage(temperature);

    Log.info("Current Resistance: %.2f, temperature %.2f, averaged temperature: %.2f",
             resistance, temperature, averaged_temperature);

    return averaged_temperature;
}

// Function to calculate the moving average of temperature samples
float calculateMovingAverage(float newTempSample)
{
    static float sumOfSamples = 0;

    if (temperatureSamples.size() >= MOVING_AVERAGE_SAMPLE_SIZE) // If the number of samples is greater than the sample size
    {
        sumOfSamples -= temperatureSamples.front(); // Subtract the first element in the queue from the sum of the samples
        temperatureSamples.pop_front();             // Remove the first element in the queue
    }

    temperatureSamples.push_back(newTempSample); // Add the new sample to the queue
    sumOfSamples += newTempSample;               // Add the new sample to the sum

    if (temperatureSamples.empty())
    {
        return 0; // If the queue is empty, average is 0
    }
    else
    {
        return sumOfSamples / temperatureSamples.size(); // Calculate the moving average of the temperature samples
    }
}

// Function to interpolate temperature from resistance using the RTD table
float interpolateTemperature(float measuredResistance)
{
    // Find the first element in the table that is greater than the measured resistance
    auto it = std::upper_bound(rtdTable, rtdTable + rtdTableSize, measuredResistance,
                               [](float a, const RtdValue &b)
                               { return a < b.resistance; }); // a is measured_resistance, b is the RtdValue struct in the table

    if (it == rtdTable + rtdTableSize) // If the measured resistance is greater than the last element in the table
    {
        return rtdTable[rtdTableSize - 1].temperature; // return the temperature of the last element in the table
    }

    if (it == rtdTable) // If the measured resistance is smaller than the first element in the table
    {
        return rtdTable[0].temperature; // return the temperature of the first element in the table
    }

    RtdValue upper = *it;     // upper is the first element in the table that is greater than the measured resistance
    RtdValue lower = *(--it); // lower is the element before upper

    return lower.temperature + (upper.temperature - lower.temperature) *
                                   (measuredResistance - lower.resistance) / (upper.resistance - lower.resistance); // Linear interpolation between lower and upper element in the table
}

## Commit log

2023-09-27 temperature PT500 sensor with Particle Argon
2023-09-27 Temperature code for PT500 sensor - Particle Argon
2023-10-11 Temperature code for PT500 sensor - Particle Argon
    Temperature updates every 20 minutes
2023-11-18 Update README.md
    Photon2 instead of Argon.
    Added actuator type.
2023-11-18 Add ValveControl and PIDController classes
2023-11-19 Add ValvePIDController for controlling valve with PID output
2023-11-19 Define PID constant
2023-12-17 Added functionality to save some data in a circular buffer and send it to Particle cloud
    Some refactorings. Fixed warning in PIDcontroller.h
    [TempSensor.cpp]
2023-12-19 Moved valve control functionallity to run in its own thread
2023-12-22 Added Docs and Tests
    [IoTSkematik2.fzz]
